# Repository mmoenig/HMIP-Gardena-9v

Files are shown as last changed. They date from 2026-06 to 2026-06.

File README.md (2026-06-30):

# Homematic IP Steuerung eines Gardena 9V Ventil

## Problem das gelöst werden soll

- Die Gardena Bewässerungscomputer mit Bluetooth lassen sich nicht zuverlässig mit dem Handy steuern.
- Die Bodenfeuchte-Sensoren die an den Ventilen angeschlossen sind funktionieren ebenfalls nicht zuverlässig. z.B. wird an Regentagen ein trockener Boden gemessen und dadurch noch zustzlich bewässert und auch in die andere Richtung wird an heissen Tagen nicht zuverlässig bewässert
- Unterschiedliche Systeme erhöhen die Komplexität und die Übersicht im SmartHome
- Gardena ist mit diesem System nicht offen und in kein anderes System integrierbar.

## High Level Requirements

- Ein Gardena 9V-Latchventil soll über das Homematic IP ansprechbar sein. 
- Die Automatisierung erfolgt (An/Ausschalten) erfolgt außerhalb dieser Schaltung über entsprechende HMiP Automatisierung
- Die Schaltung muss mit 4 AA-Zellen für 6 Monate lauffähig sein (Garten-Saison)
- Die Ganze Elektronik soll in einer relativ kleinen Abzweigdose (Spelsberg Abox 025) untergebracht werden
- Die Schaltung soll nur für ein einzelnes Ventil sein

## Hardware Komponenten

Die Steuerung basiert auf:

* [Homematic IP HMIP-PCBS-BAT als Funkmodul](hardware/hmippcbsbat/hmippcbsbat.md)
* [Gardena 9V Ventil](hardware/gardena/gardena.md)
* [ATtiny85 als Steuerlogik](hardware/ATtiny85/attiny85.md) 
* [DRV8833 als H-Brücke](hardware/drv8833/drv8833.md)
* [MT3608 als Step-up Wandler](hardware/mt3608/mt3608.md)
* [Spelsberg Abox 025 als Gehäuse](hardware/abox025/abox025.md)
* 4× AA Batterieversorgung (LifePo4)

## Materialliste

| Pos. | Bauteil | Typ / Wert | Menge | Bemerkung |
| ---: | --- | --- | ---: | --- |
| 1 | Funk-Schaltaktor | HmIP-PCBS-BAT | 1 | Homematic IP Schaltplatine |
| 2 | Mikrocontroller | ATTiny85-20PU | 1 | DIP-8 Sockel |
| 3 | Motortreiber | [DRV8833 Modul](https://www.amazon.de/DRV8833-2-Kanal-DC-Motorantriebsplatine-Motorantriebs-Eingangsspannung/dp/B0DHRFRG6X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) | 1 | H-Brücke für Polaritätsumkehr |
| 4 | Step-Up-Wandler | [MT3608 Modul](https://www.amazon.de/Converter%EF%BC%8CEinstellbare-Spannungsreglerplatine-Power2V-24V-V%EF%BC%8CNetzteil-Kompatibel/dp/B0D9VJKD1L/) | 1 | Eingang 4–6 V, Ausgang 9 V |
| 5 | Bewässerungsventil | Gardena 01815-00.707.00 | 1 | Hydraulikventil mit Cinch-Anschluss |
| 6 | Batteriehalter | 2× AA | 2 | 1 x HMIP und 1 x Lastkreis (DRV8833,ATTiny,MT3608) |
| 7 | Batterie | [AA LiFePO4, 3.2V 600mAh](https://www.amazon.de/POWJIELI-Wiederaufladbarer-Selbstentladung-Solar-Gartenleuchten-Solarpfostenleuchten/dp/B0FLWY2FXT) | 4 | Versorgung |
| 8 | Widerstand | 10 kΩ | 1 | Pull-Up für HmIP-Ausgang |
| 9 | Widerstand | 47 Ω | 1 | Strombegrenzung Schließimpuls |
| 10 | Diode | 1N4001 | 1 | Überbrückung des 47-Ω-Widerstands |
| 11 | Kondensator | 670 µF / ≥16 V | 1 | MT3608 Eingang |
| 12 | Kondensator | 100 µF / ≥16 V | 1 | DRV8833 Versorgung |
| 13 | Kondensator | 100 nF | 2 | DRV8833 und ATTiny85 |
| 14 | IC-Sockel | DIP-8 | 1 | Für ATTiny85 |
| 15 | Terminal-Anschlussblock | [10 alt. 12 fach, 2.54](https://www.amazon.de/10Pcs-Terminal-Block-Steckverbinder-Schraubklemmenblock/dp/B07BVPJBK3) | 1 | Gardena Ventil, Batterie, HMIP |
| 17 | Gehäuse | Spelsberg ABOX 025 | 1 | Endmontage |
| 18 | Lochrasterplatine  | 24 Spalten (A–X),2.54 | 1 | Individuell zuschneiden |
| 19 | Silberdraht | 0,14–0,25 mm² | nach Bedarf | Verdrahtung |
| 20 | Schrumpfschlauch | verschiedene Größen 1,5 / 3.5 /4.0 | nach Bedarf | Isolation |

## Schaltung - Komponentensicht

### Gardena Aktor
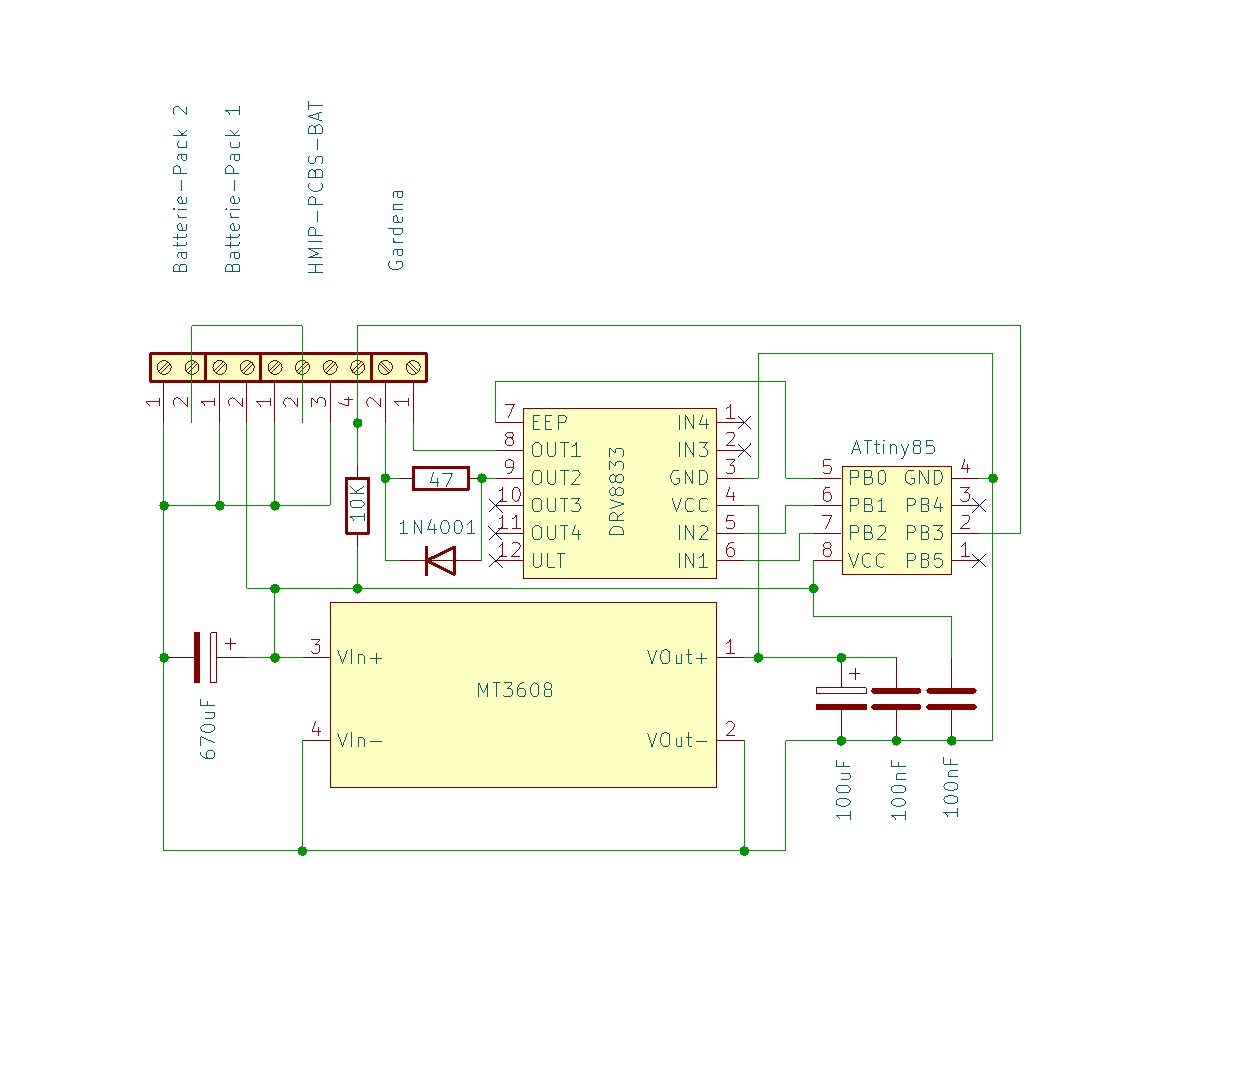
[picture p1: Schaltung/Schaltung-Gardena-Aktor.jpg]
Schaltung-Aktor


### Homematic IP
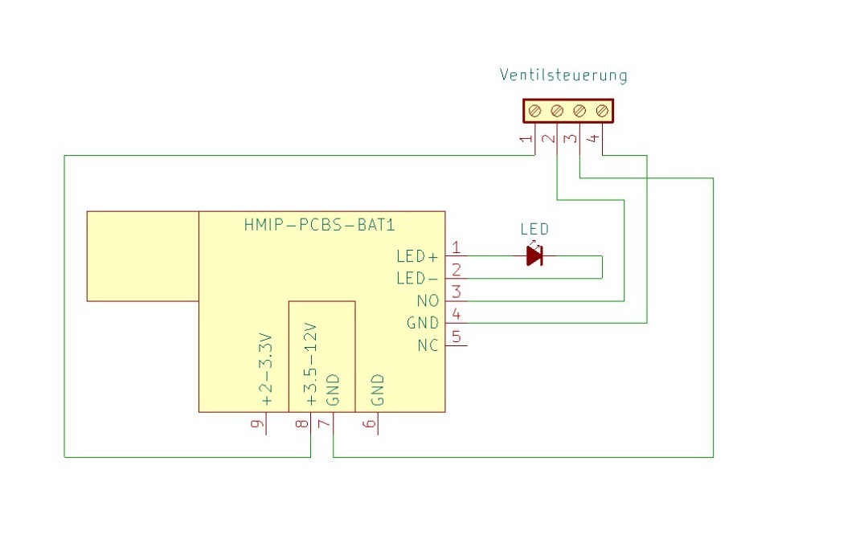
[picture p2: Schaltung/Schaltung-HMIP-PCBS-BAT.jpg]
Schaltung-HMIP


## Architektur
~~~
                    Gemeinsame Masse (GND)
                           │
        ┌──────────────────┴──────────────────┐
        │                                     │

   Batteriepack 1                       Batteriepack 2
      (Logik)                            (Leistung)
      2×AA / 6–7 V                       2×AA / 6–7 V
        │                                     │
        │                                     ├──────── ATTiny85
        │                                     ├──────── MT3608
        │                                     │
        │                                     └── MT3608 ── 9 V ── DRV8833 ── Gardena Ventil
        │
        └──────── HmIP-PCBS-BAT

HmIP Open-Drain Ausgang ───────────────► PB3 (ATTiny)
~~~

## Funktionsprinzip

Das Homematic-IP-Modul liefert ein digitales Open-Drain-Triggersignal an den ATTiny85.

Der ATTiny85 überwacht den Eingang kontinuierlich und erkennt jede Zustandsänderung (LOW→HIGH bzw. HIGH→LOW). Abhängig von der Richtung der Zustandsänderung erzeugt er einen kurzen Steuerimpuls:

Öffnen: 60 ms
Schließen: 250 ms

Der DRV8833 arbeitet als H-Brücke und kehrt für jeden Steuerimpuls die Polarität um. Dadurch kann das bistabile 9-V-Gardena-Magnetventil sowohl geöffnet als auch geschlossen werden.

## Stromversorgung

### Batterieversorgung

| Versorgung | Spannung | Versorgt |
| --- | --- | --- |
| Batteriepack 1 | 2× LiFePO₄ (6,0–7,2 V) | ATTiny85, MT3608, DRV8833 |
| Batteriepack 2 | 2× LiFePO₄ (6,0–7,2 V) | HmIP-PCBS-BAT |

### Spannungsverteilung

| Komponente | Versorgung |
| --- | --- |
| ATTiny85 | direkt aus Batterie |
| HmIP-PCBS-BAT  | direkt aus Batterie |
| MT3608 Eingang | direkt aus Batterie |
| DRV8833 | 9V vom MT3608 |
| Ventil | 9V vom DRV8833 |

### Masseverteilung

Eine gemeinsame Masse - keine getrennten Massebereiche erforderlich.
~~~
Batteriepack 1 (+6 V)
    │
    ├── ATTiny85
    ├── MT3608
    └── DRV8833

Batteriepack 2 (+6 V)
    │
    └── HmIP-PCBS-BAT

Gemeinsame Masse (GND)
    ├── Batteriepack 1
    ├── ATTiny85
    ├── MT3608
    ├── DRV8833
    ├── HmIP-PCBS-BAT
    └── Batteriepack 2
~~~

## MT3608 Step Up Wandler

Der MT3608 erhöht die Batteriespannung auf 9V für:

- DRV8833
- Gardena-Ventil

| Parameter | Wert |
| --- | ---- |
| Ausgangsspannung | 9V |

**WICHTIG*** 
Vor Inbetriebnahme die Ausgangsspannung mit Multimeter einstellen!

## HmIP-PCBS-BAT Homematic IP Funkmodul

Das Modul liefert ein Open-Drain-Schaltsignal an den ATTiny85.

| Zustand | Ausgang |
| --- | --- |
| aktiv | LOW |
| inaktiv | offen |

### Pin Belegung

| Pin | Funktion | Verbindung |
| --- | --- | --- |
| NO | Open-Drain-Ausgang | Normally Open, ATTiny85 PB3, 10 KOhm Pullup Widerstand gegen VCC |
| NOC | Open-Drain-Ausgang | - |
| GND | Masse | gemeinsame Masse |
| +3.5-12V | Versorgung | Batteriespannung |
| LED+ | LED | LED + |
| LED- | LED | LED - |

### Schaltung
~~~
6.4V (VCC)
 │
 └── 10kΩ
       │
       ├──── ATTiny85 PB3
       │
HmIP-PCBS-BAT OUT
       │
      GND
~~~

## ATTiny85 Steuerlogik

Der ATTiny85 übernimmt:

- Flankenerkennung
- Impulssteuerung
- Polaritätssteuerung
- Sleep-Modus

### Pin Belegung

| ATTiny85 Pin | Port | Funktion |
| --- | ---- | --- |
| 1 | PB5  | - |
| 2 | PB3  | Trigger Eingang |
| 3 | PB4  | - |
| 4 | GND  | Masse |
| 5 | PB0  | DRV8833 SLP/EEP |
| 6 | PB1  | DRV8833 IN2 |
| 7 | PB2  | DRV8833 IN1 |
| 8 | VCC  | 6.4V |

## DRV8833 H-Brücke

Der DRV8833 erzeugt:

- positive Polarität
- negative Polarität

für das bistabile Gardena-Ventil.

### Pin Belegung

| Pin | Funktion | Verbindung |
| ----- | --- | --- |
| VCC | Ventilversorgung  | 9V vom MT3608 |
| GND | Masse | gemeinsame Masse |
| IN1 | Richtung A | ATTiny85 PB2 |
| IN2 | Richtung B | ATTiny85 PB1 |
| IN3 | unbenutzt | - |
| IN4 | unbenutzt | - |
| OUT1  | Ventilanschluss A | Gardena 1 | 
| OUT2  | Ventilanschluss B | Gardena 2 |
| OUT3  | unbenutzt | - |
| OUT4  | unbenutzt | - |
| EEP | Sleep-Eingang | ATTiny85 PB0 |
| FAULT | Fehlerausgang | - |

### Schaltung

~~~
VCC ---- 100µF (Elko) ----- GND
  \
   \--- 100nF (Keramik) --- GND
~~~

- Elko zur Stabilisierung der 9V Versorgung
- Kermatik Kondesator kann sehr schnell reagieren zur Filterung von schnelle Spannungsspitzen, Schaltflanken, HF-Störungen

## Gardena 9V Ventil

## Ventil schließen

| Signal | Zustand |
| --- | --- |
| IN1 | LOW |
| IN2 | HIGH |
| Dauer  | 250 ms  |

## Ventil öffnen

| Signal | Zustand |
| --- | --- |
| IN1 | HIGH |
| IN2 | LOW |
| Dauer  | 60 ms |

## Software / Steuerungslogic ATtiny85

* [Software Page](./Software/Sketch.md)

## Design-Werkzeuge

- KiCad 10.0, Schaltungs-Entwurf, https://www.kicad.org/
- Ardunino IDE 2.3.9, Sketch Entwicklung, https://docs.arduino.cc/software/ide/
- Trimble Sketchup for Web, 3D Modell Entwicklung, https://app.sketchup.com/app
- BambuLab 2.7.1.57, Slicer, https://bambulab.com/en/download/studio
- Fritzing 1.0.7, Lochraster Design, https://fritzing.org/download/

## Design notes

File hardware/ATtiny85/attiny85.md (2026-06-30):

# Atmel 8-Bit-AVR-Mikrocontroller mit 8K Byte In-System programmierbarem Flash

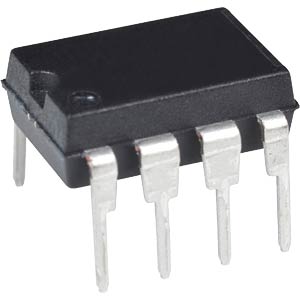
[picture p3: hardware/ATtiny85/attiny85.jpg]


## Merkmale:
- Hochleistungs-, stromsparender AVR® 8-Bit-Mikrocontroller
- Fortgeschrittene RISC-Architektur
- 120 leistungsstarke Anweisungen - die meisten Ein-Takt-Zyklus-Ausführungen
- 32 x 8 Arbeitsregister für allgemeine Zwecke
- Vollständig statischer Betrieb
- Nichtflüchtige Programm- und Datenspeicher
- 8K Byte systeminterner programmierbarer Programmspeicher Flash, 10.000 Schreib-/Löschzyklen
- 512 Bytes In-System programmierbares EEPROM, 100.000 Schreib-/Löschzyklen
- 512 Bytes interner SRAM
- Programmiersperre für selbstprogrammierendes Flash-Programm und EEPROM-Datensicherheit

### Periphere Merkmale
- 8-Bit-Timer/-Zähler mit Vorteiler und zwei PWM-Kanälen
- 8-Bit-Hochgeschwindigkeits-Zeitgeber/-Zähler mit separatem Vorteiler
- 2 Hochfrequenz-PWM-Ausgänge mit getrennten Ausgangs-Vergleichsregistern
- Programmierbarer Totzeit-Generator
- USI - Universelle serielle Schnittstelle mit Startbedingungsdetektor
- 10-Bit-ADC
- 4 Kanäle mit einem Ende
- Differentielle ADC-Kanalpaare mit programmierbarer Verstärkung (1x, 20x)
- Temperaturmessung
- Programmierbarer Watchdog-Timer mit separatem On-Chip-Oszillator
- On-Chip-Analogkomparator
- Industrieller Temperaturbereich

### Besondere Mikrocontroller-Merkmale
- debugWIRE On-chip-Debug-System
- Im System über SPI-Port programmierbar
- Externe und interne Interrupt-Quellen
- Niedrigleistungs-Leerlauf, ADC-Rauschunterdrückung und Abschaltmodi
- Erweiterte Power-on-Reset-Schaltung
- Programmierbare Brown-out-Erkennungsschaltung
- Intern kalibrierter Oszillator

### E/A und Bauformen
- Sechs programmierbare E/A-Leitungen
- 8-polige PDIP, 8-poliger SOIC, 20-poliges QFN/MLF

### Betriebsspannung
- 1,8 - 5,5V für ATtiny85V
- 2,7 - 5,5V für ATtiny85

### Geschwindigkeits-Grad
- ATtiny85V: 0 - 4 MHz bei 1,8 - 5,5V, 0 - 10 MHz bei 2,7 - 5,5V
- ATtiny85: 0 - 10 MHz bei 2,7 - 5,5V, 0 - 20 MHz bei 4,5 - 5,5V, 0 - 20 MHz bei 4,5 - 5,5V

### Leistungsaufnahme
- Aktiver Modus: 1 MHz, 1,8V: 300 µA
- Abschaltmodus: 0,1 µA bei 1,8V

## Pin Belegung
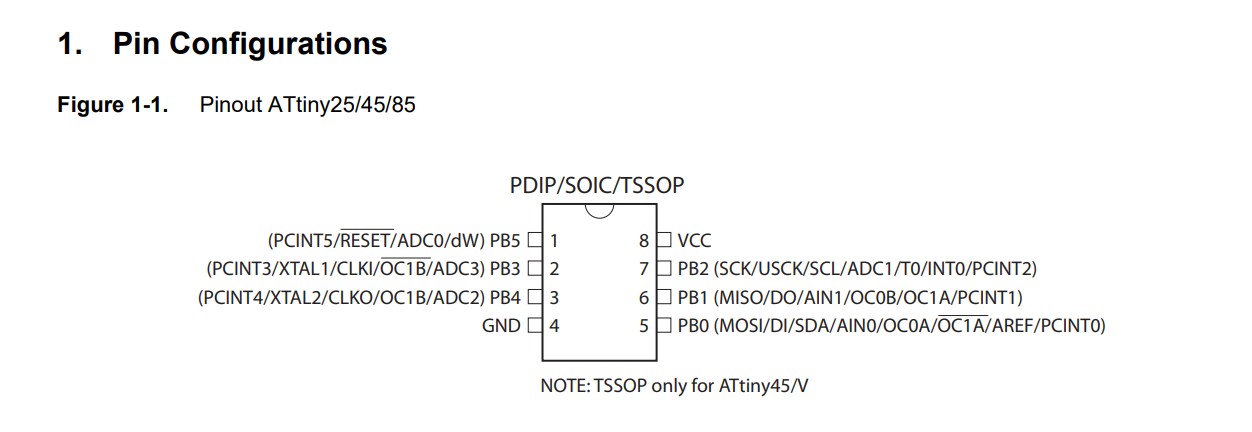
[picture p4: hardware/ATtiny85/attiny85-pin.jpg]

## Datenblatt
[Datenblatt](./attiny85.pdf)

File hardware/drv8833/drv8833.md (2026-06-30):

# DRV8833 1.5A 2-Kanal H Brücke DC-Motorantriebsplatine Ultra Small Volume Motorantriebs modul

- Der Motortreiber kann bei einem Konstantstrom von 1,0 A (4 A Spitze) bis zu zwei DC-Motoren steuern.
- Zwei Eingangssignale (IN1 und IN2) können verwendet werden, um den Motor in einem von vier Funktionsmodi zu steuern – Uhrzeigersinn (CW), gegen den Uhrzeigersinn (CCW), kurze Pause und Stopp.
- Eingebauter Überstromschutz, Kurzschlussschutz, Unterspannungsabschaltung und Übertemperaturschutz. Im Energiesparmodus.
- Die zwei Motorenausgänge (A und B) können separat gesteuert werden, die Geschwindigkeit jedes Motors wird über ein PWM-Eingangssignal mit einer Frequenz bis zu 100 kHz gesteuert.

## Netzstrom 
- VM = 2,7–10,8 V.
- Ausgangsstrom: Iout = 1,0 A (Durchschnitt) / 4 A (Spitze).

## DRV8833 Merkmale

| Eigenschaft | Wert |
| --- | --- |
| Versorgung VM | 2.7V – 10.8V |
| Sleep-Strom | typ. 1.6 µA |
| H-Brücken | 2 |
| Ausgangsstrom | 1.5A RMS / 2A Peak |
| Technologie | MOSFET |
| Polaritätsumkehr | ja |
| Schutzfunktionen | Überstrom, Temperatur, UVLO |
| Eingangskompatibilität | 3.3V / 5V GPIO |

## Datenblatt
[Datenblatt](./drv8833.pdf)

## Bilder
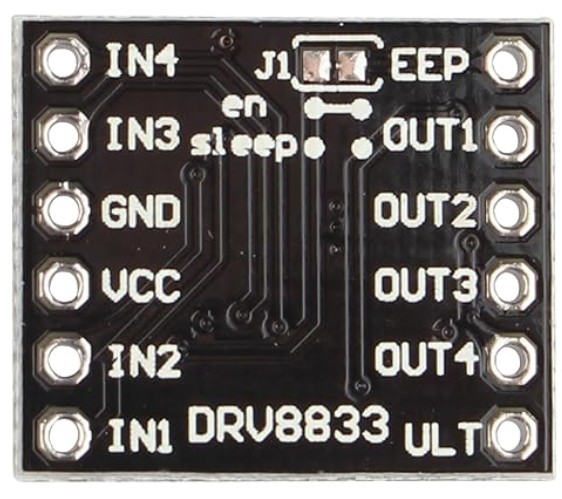
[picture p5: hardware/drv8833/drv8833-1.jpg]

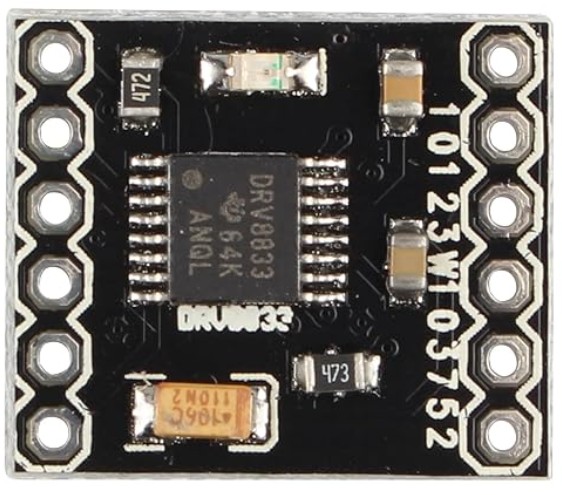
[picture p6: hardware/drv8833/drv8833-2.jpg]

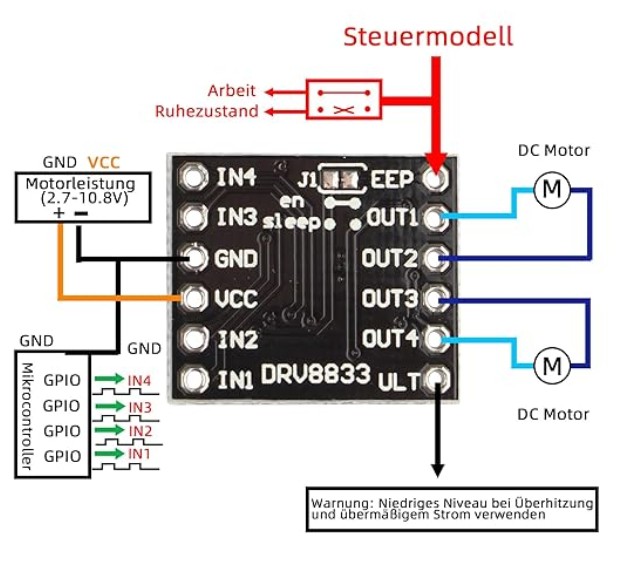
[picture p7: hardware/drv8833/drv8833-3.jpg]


## Pin Belegung

| Pin | Richtung | Funktion | Anschluss |
| ----- | --- | --- | --- |
| VCC | Eingang  | Versorgung DRV8833 (2.7–10.8V) | 9V vom MT3608 |
| GND | Eingang  | Masse | Gemeinsame GND |
| IN1 | Eingang  | Steuerung Kanal A Richtung 1 | ATTiny85 PB2 |
| IN2 | Eingang  | Steuerung Kanal A Richtung 2 | ATTiny85 PB1 |
| IN3 | Eingang  | Steuerung Kanal B Richtung 1 | - |
| IN4 | Eingang  | Steuerung Kanal B Richtung 2 | - |
| OUT1  | Ausgang  | Kanal A Ausgang 1 | Ventil 1 Leitung A |
| OUT2  | Ausgang  | Kanal A Ausgang 2 | Ventil 1 Leitung B |
| OUT3  | Ausgang  | Kanal B Ausgang 1 | - |
| OUT4  | Ausgang  | Kanal B Ausgang 2 | - |
| SLP | Eingang  | Sleep-Steuerung | ATTiny85 PB0. |
| FAULT | Ausgang  | Fehlerausgang | Optional / offen |

## Truth Table

(OUT1 und OUT2) sowie (OUT3 und OUT4) gehören fest zu einer H-Brücke und können nicht unabhängig voneinander verwendet werden.

| IN1 | IN2 | Ausgang |
| --- | --- | --- |
| 1 | 0 | OUT1=H / OUT2=L |
| 0 | 1 | OUT1=L / OUT2=H |
| 0 | 0 | Hi-Z / Coast |
| 1 | 1 | Brake |

| IN1  | IN2  | OUT1 | OUT2 |
| ---- | ---- | ---- | ---- |
| HIGH | LOW  | +9V  | GND  |
| LOW  | HIGH | GND  | +9V  |

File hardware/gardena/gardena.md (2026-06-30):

# Gardena 1251-20 9V Ventil

# Beschreibung

Das Bewässerungsventil ist bistabil, d.h. es benötigt einen Stromimpuls zum Öffnen und einen weiteren um wieder zu schließen.

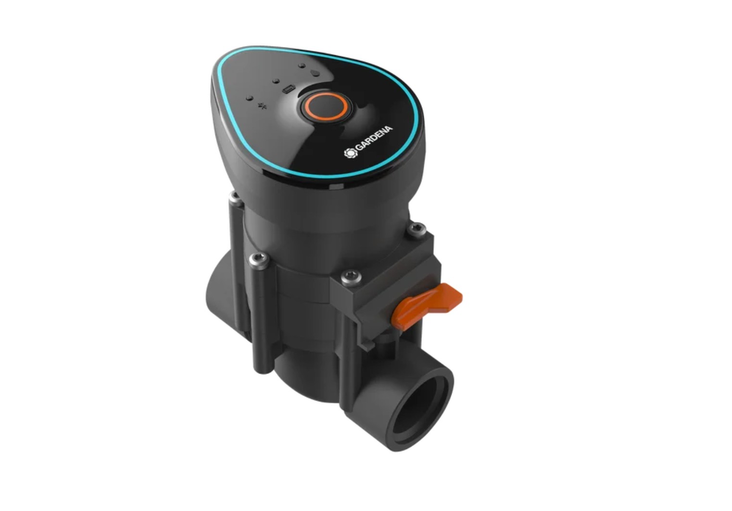
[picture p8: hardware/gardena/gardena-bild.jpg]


# Ansteuerung

Für Gardena 9 V bistabile Ventile gilt:

|Funktion |Spannung |Strom |Zeit |
|---|---|---|---|
|Öffnen	 |+9 V	 |~250–350 mA	 |~250 ms |
|Schließen |-9 V	 |~20–80 mA	 |~62,5 ms |

**Wichtig: Der Strom muss beim Schließen auf 80mA begrenzt werden sonst schließt das Ventil nicht!**

* [Gardena Technische Information](https://help.gardena.com/hc/de/articles/4450459219100-Welche-technischen-Daten-hat-das-9-V-Bew%C3%A4sserungsventil)

Die technischen Daten passen auch für die Bewässerungscomputer (Gardena Bluetooth) Artikel-Nr. 1889-20
- https://www.gardena.com/de/produkte/bewaesserung/bewaesserungssteuerung/bewaesserungssteuerung-bluetooth/970481101.html

# Dokumente

* [Ersatzteile](./gardena-ersatzteile.pdf)
* [Handbuch](./gardena-handbuch.pdf)
* [Ventil-Handbuch](./gardena-ventil.pdf)
* [Forum](https://homematic-forum.de/forum/viewtopic.php?f=19&t=2971#p15995)
* [Raspberry Forum](https://forum-raspberrypi.de/forum/thread/42577-umbau-gardena-bewaesserungsventil-1251-20-9v-auf-homematic/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)

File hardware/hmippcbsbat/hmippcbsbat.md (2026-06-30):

# Homematic IP Schaltaktor HMIP-PCBS-BAT für Batteriebetrieb

Baut man ein Smart Home Systems auf, steht man früher oder später unweigerlich vor der Aufgabe, eine Fernsteuerung weit ab von einer Netzstromversorgung ausführen zu wollen. Dann muss man auf Batterien, Akkus oder Solarzellen als Stromversorgung setzen. Genau dies ist der Einsatzort der neuen Schaltplatine für Batteriebetrieb. Aufgrund ihrer geringen Größe und ihres geringen Stromverbrauchs ist sie einfach in eigene Applikationen integrierbar.

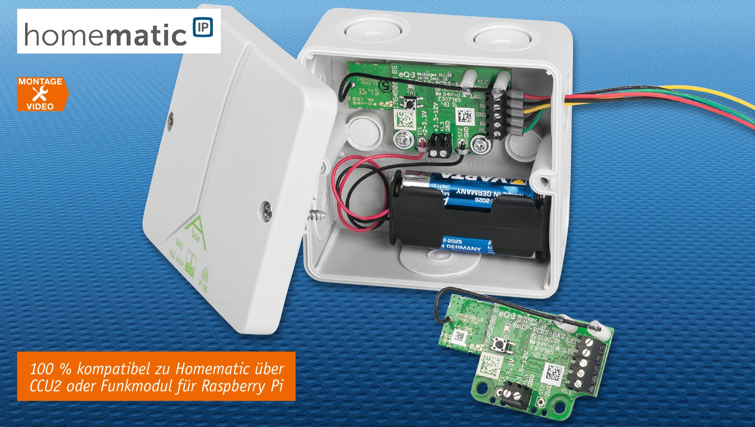
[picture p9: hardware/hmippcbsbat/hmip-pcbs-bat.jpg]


## Merkmale

| Eigenschaft | Wert |
| --- | --- |
| Geräte-Kurzbezeichnung | HmIP-PCBS-BAT |
| Versorgungsspannung | 2–3,3 VDC / 3,5–12 VDC |
| Stromaufnahme | max. 40 mA |
| Ausgänge | 2× Open-Drain 20 V / 3 A |
| Ausgangszustände | 1× in Ruhe offen / 1× in Ruhe geschlossen |
| Zusätzlicher Ausgang | 1× LED-Ausgang |
| LED-Betrieb | mit integriertem oder externem Vorwiderstand |
| Besonderheit | für stromsparenden Batterie-/Akkubetrieb optimiert |
| Leitungsart | starre oder flexible Leitung |
| Leitungsquerschnitt | 0,75–1,0 mm² |
| Maximale Leitungslänge | 3 m |
| Umgebungstemperatur | -10 bis +55 °C |
| Schutzklasse | III |
| Verschmutzungsgrad | 2 |
| Abmessungen (B × H × T) | 60 × 34 × 17 mm |
| Gewicht | 11 g |
| Funkmodul | TRX1-TIF |
| Funkfrequenzband | 868,0–868,6 MHz / 869,4–869,65 MHz |
| Funksendeleistung | max. 10 dBm |
| Empfängerkategorie | SRD category 2 |
| Typische Funkreichweite Freifeld | 250 m |
| Duty Cycle | < 1 % pro h / < 10 % pro h |

## Bilder

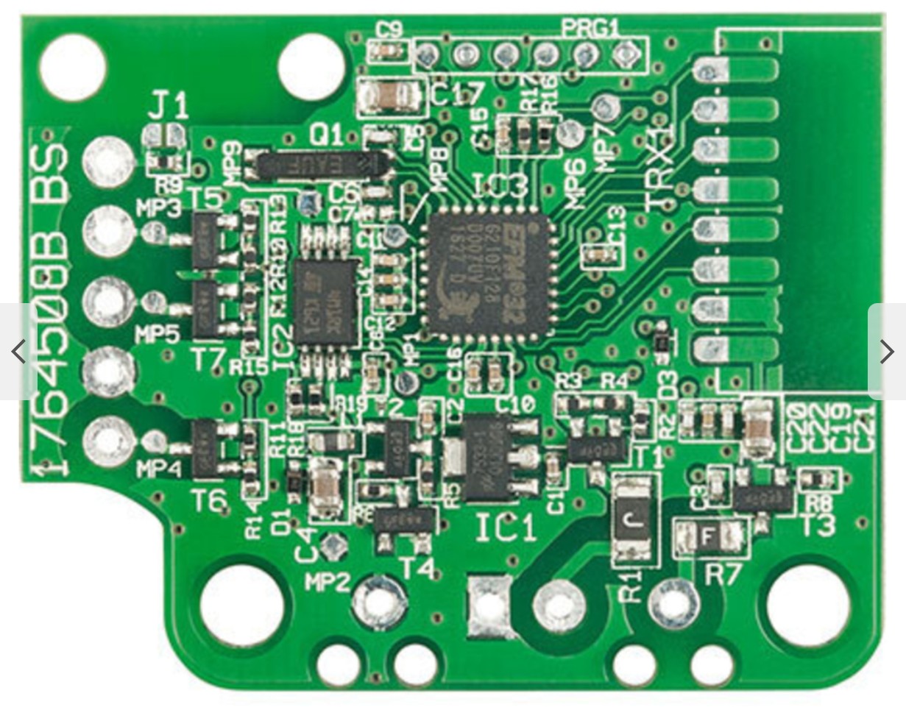
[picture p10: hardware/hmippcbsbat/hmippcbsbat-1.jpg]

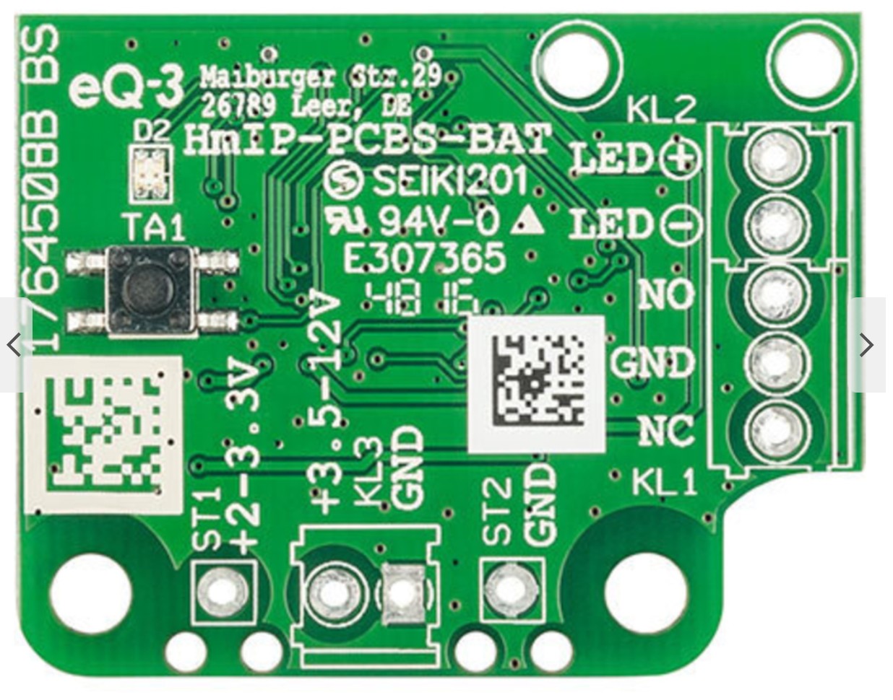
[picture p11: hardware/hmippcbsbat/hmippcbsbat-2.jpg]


## Schaltung

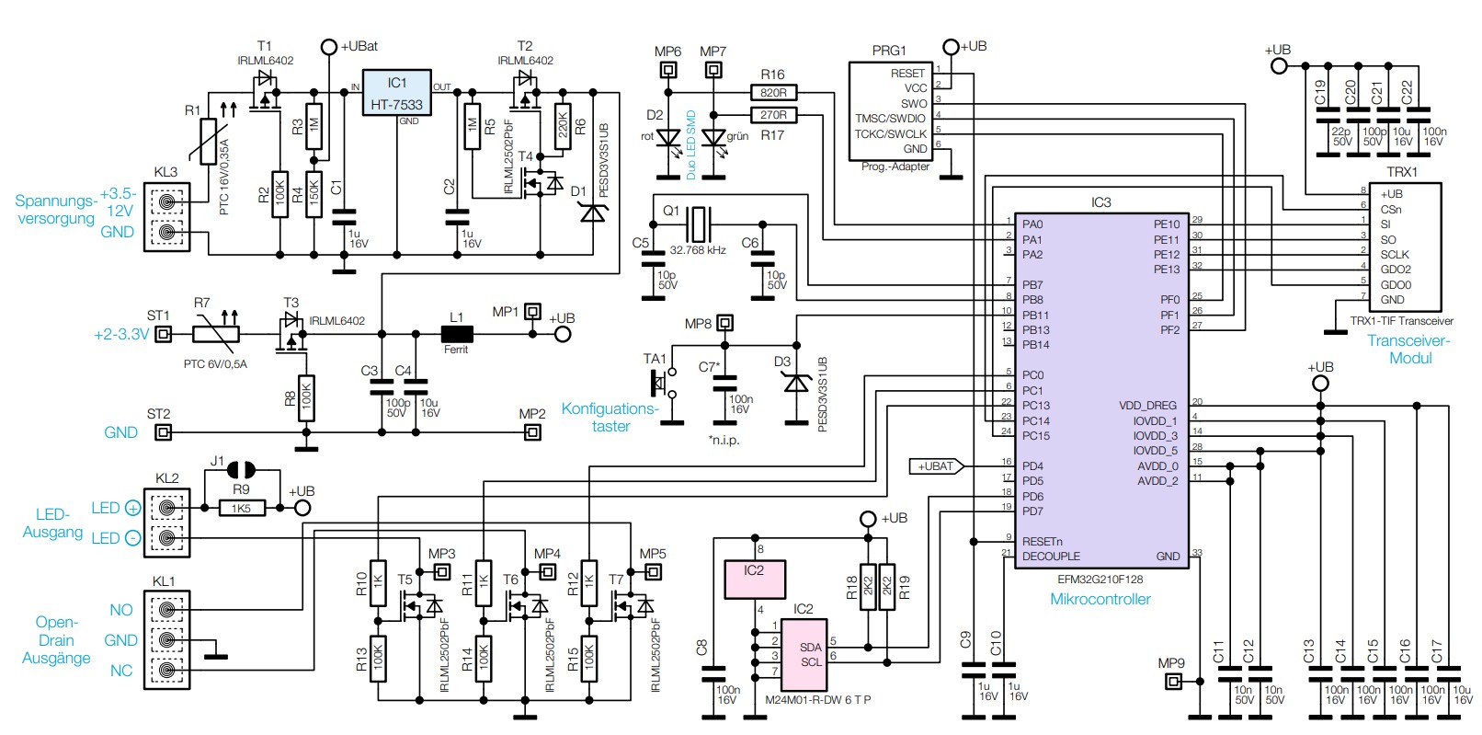
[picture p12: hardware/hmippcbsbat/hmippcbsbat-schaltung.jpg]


## Referenzen

- [ELV Produktseite](https://de.elv.com/p/homematic-ip-ganz-flexibel-schaltplatine-hmip-pcbs-bat-fuer-batteriebetrieb-P207141/?itemId=207141)
- [Schaltplan](./hmippcbsbat-schaltung.pdf)
- [ELV Artikel](./hmippcbsbat-journal.pdf)

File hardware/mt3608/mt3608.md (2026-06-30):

# MT3608 Mini DC-DC-Step up Wandler

Der MT3608 ist ein 2-A-DC/DC-Aufwärtswandlermodul (Boost-Wandler), das Eingangsspannungen von nur 2 V auf eine einstellbare Ausgangsspannung von bis zu 28 V hochwandeln kann. Es zeichnet sich durch einen Wirkungsgrad von 97 %, eine Schaltfrequenz von 1,2 MHz und eine integrierte Soft-Start-Technologie aus. Auch im Jahr 2026 gilt es aufgrund seiner geringen Kosten und des SOT-23-Formfaktors weiterhin als Goldstandard für die Stromversorgung von Arduino-, ESP32- und IoT-Projekten über Li-Ionen-Akkus.

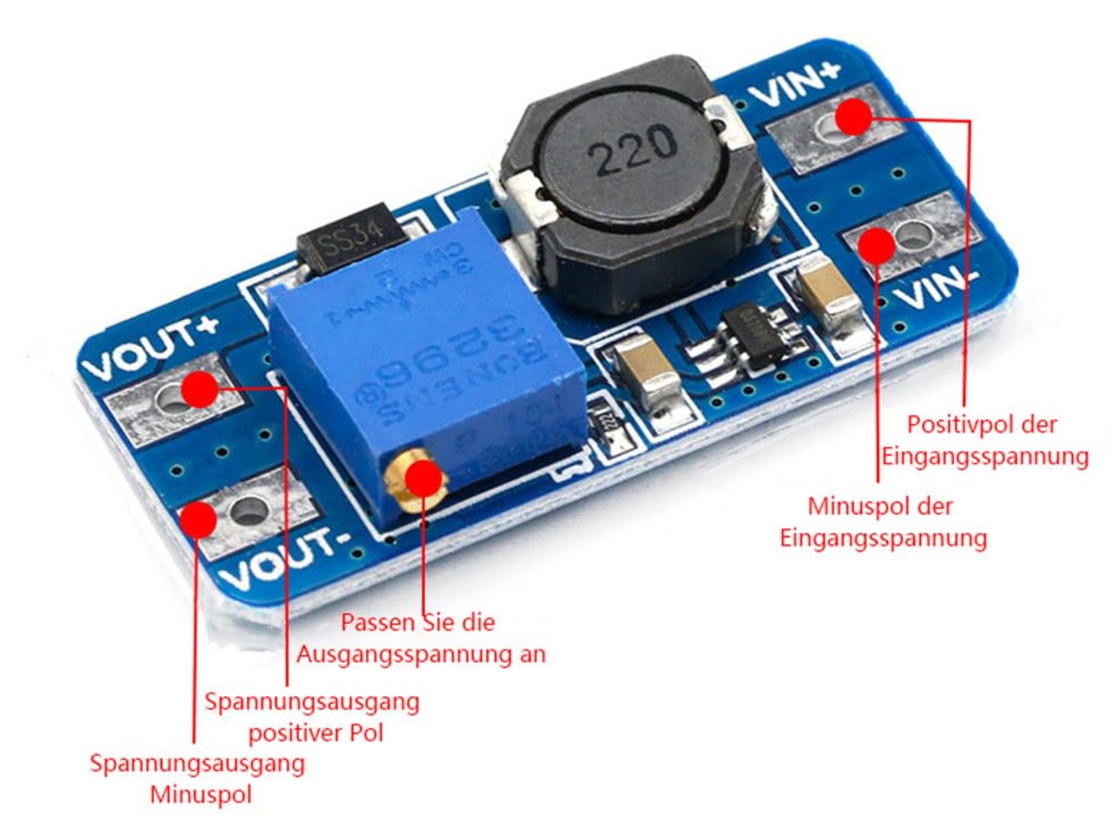
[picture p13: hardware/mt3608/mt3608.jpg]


## Technische Eigenschaften

| Eigenschaft | Wert |
| --- | --- |
| Typ | DC/DC Step-Up Converter |
| Funktion | Spannungsaufwärtswandler |
| Eingangsspannung | 2V – 24V |
| Ausgangsspannung | bis 28V |
| Ausgangsstrom | typ. bis 2A |
| Wirkungsgrad | bis ca. 93–97 % |
| Schaltfrequenz | 1.2 MHz |
| Ruhestrom | typ. 100–200 µA |
| Shutdown-Strom | typ. 0.1 µA |
| Schutzfunktionen | Überstrom, Übertemperatur, UVLO |
| Gehäuse IC | SOT23-6 |
| Regelung | PWM/PFM |

## Pinbelegung

| Modulanschluss | Funktion |
| --- | --- |
| VIN+ | Eingang + |
| VIN- | Eingang GND |
| VOUT+ | Ausgang + |
| VOUT- | Ausgang GND |

## Referenzen
- [mt3608 Datenblatt](./mt3608.pdf)

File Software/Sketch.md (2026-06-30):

# Software für die Gardena Ventilschaltung (ATtiny85)

* [ArduninoISP.ino](./ArdunioISP.ino)
* [HomematicIPGardena.ino](./HomematicIPGardena.ino)

Zusätzliche Boardverwalter URL für Arduino IDE:
- https://raw.githubusercontent.com/damellis/attiny/ide-1.6.x-boards-manager/package_damellis_attiny_index.json
- https://github.com/damellis/attiny

# Software flashen

## Vorbereitung Arduino IDE
### ATtiny libs in Arduino IDE hinzufügen

1. Arduino IDE (hier 2.3.9) starten
2. Datei > Einstellungen > Zusätzliche Boardverwalter-URLs auswählen. Oben genannte URL einfügen. > OK
3. Öffnen des Boardverwalters unter Werkzeuge > Board > Boardverwalter.
4. attiny von David A. Mellis (hier 1.0.2) installieren

### Arduino UNO als Programmierer einrichten

1. Arduino UNO mit USB an Rechner anschließen
2. Arduino IDE starten
3. Datei > Beispiele > ArduinoISP > ArduinoISP
4. Im Pulldown Menü Arduino UNO am entsprechenden COM Port auswählen
5. Sketch auf Arduino UNO hochladen

## Hardware vorbereiten
### Attiny für Flashvorgang verkabeln

Den ATtiny85 wird mit einem Arduino UNO als Programmierer (ISP) geflasht.
Dazu wird der ATtiny85 auf ein Breadboard gesteckt und folgende Pins mit dem Arduino UNO verbunden.

| Arduino Uno | ATTiny85 Pin |
| --- | --- |
| D10 | Pin 1 (RESET) |
| D11 | Pin 5 (PB0/MOSI) |
| D12 | Pin 6 (PB1/MISO) |
| D13 | Pin 7 (PB2/SCK)  |
| 5V | Pin 8 (VCC) |
| GND | Pin 4 (GND) |

Ein 10yF Elko muss zwischen Pin 1 und GND eingebaut werden.

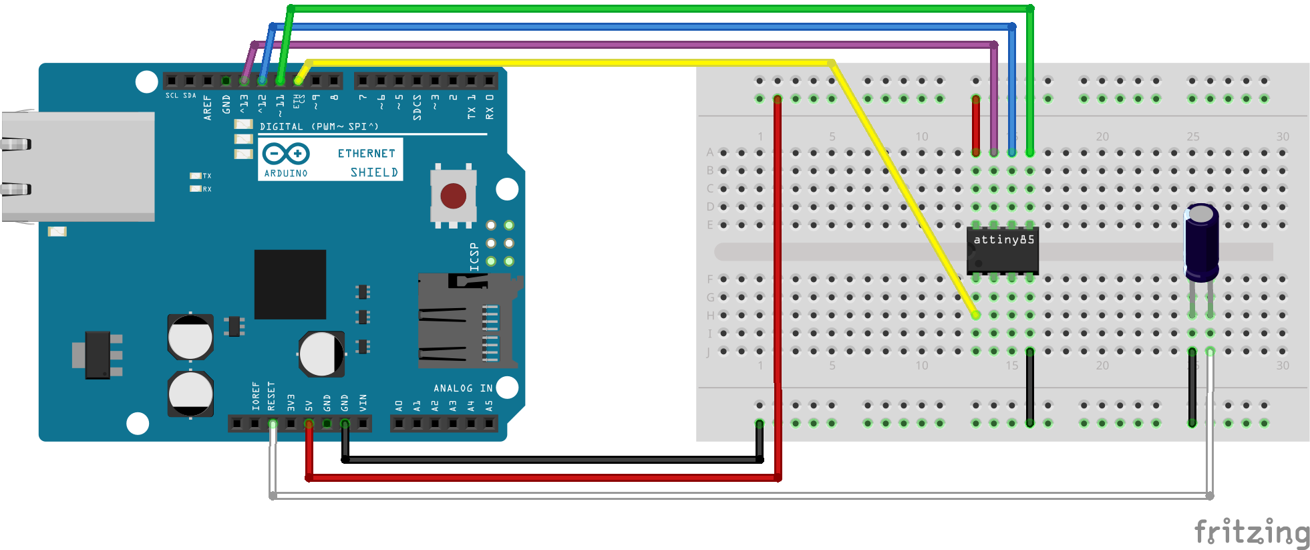
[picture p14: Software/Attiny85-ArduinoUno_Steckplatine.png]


## Software hochladen
### Program auf ATtiny85 schreiben

1. Arduino IDE öffnen und Gardena Sketch laden
2. Attiny25/45/85 Board am entsprechenden COM port auswählen
3. Taktfrequenz einstellen: Werkzeuge > Clock: Internal 1 MHz ausählen
4. Prozessor einstellen: Werkzeuge > Prozessor > ATtin85 auswählen
5. Programmier Methode einstellen: Werkzeuge > Programmer > ArduinoISP als Programmer auswählen
6. Upload durchführen: **Wichtig** Sketch > Mit Programmer hochladen

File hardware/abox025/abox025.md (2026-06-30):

# Spelsberg Abox 025

Abzweigkasten, mit Schutzart IP66, Nennquerschnitt 2,5 mm², zertifiziert durch VDE (DIN EN 60670-1/-22 (VDE 0606-1/-22)), DLG (Ammoniakbeständigkeit), selbstdichtende, weiche Einführungsmembranen, M16/M20, Dichtbereich 4 - 16 mm, (1 rückseitig, 8 seitlich), innenliegende Befestigungsstellen, für Standardinstallationen im Innenbereich und geschütztem Außenbereich

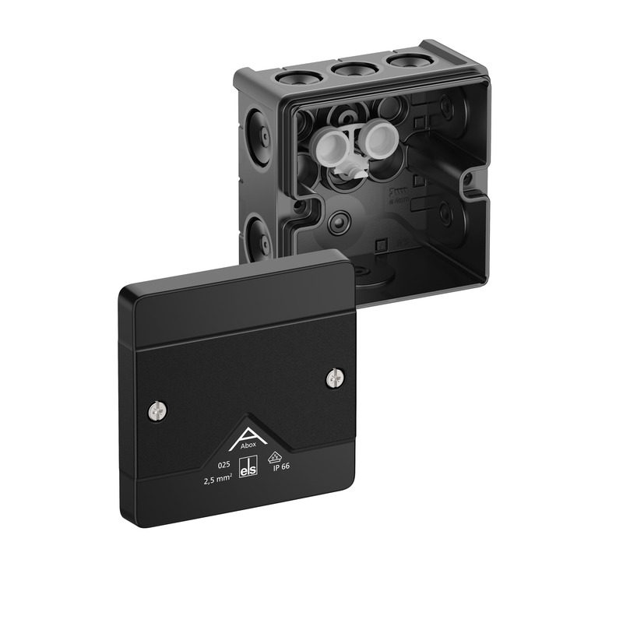
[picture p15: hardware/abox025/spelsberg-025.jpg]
Abox025


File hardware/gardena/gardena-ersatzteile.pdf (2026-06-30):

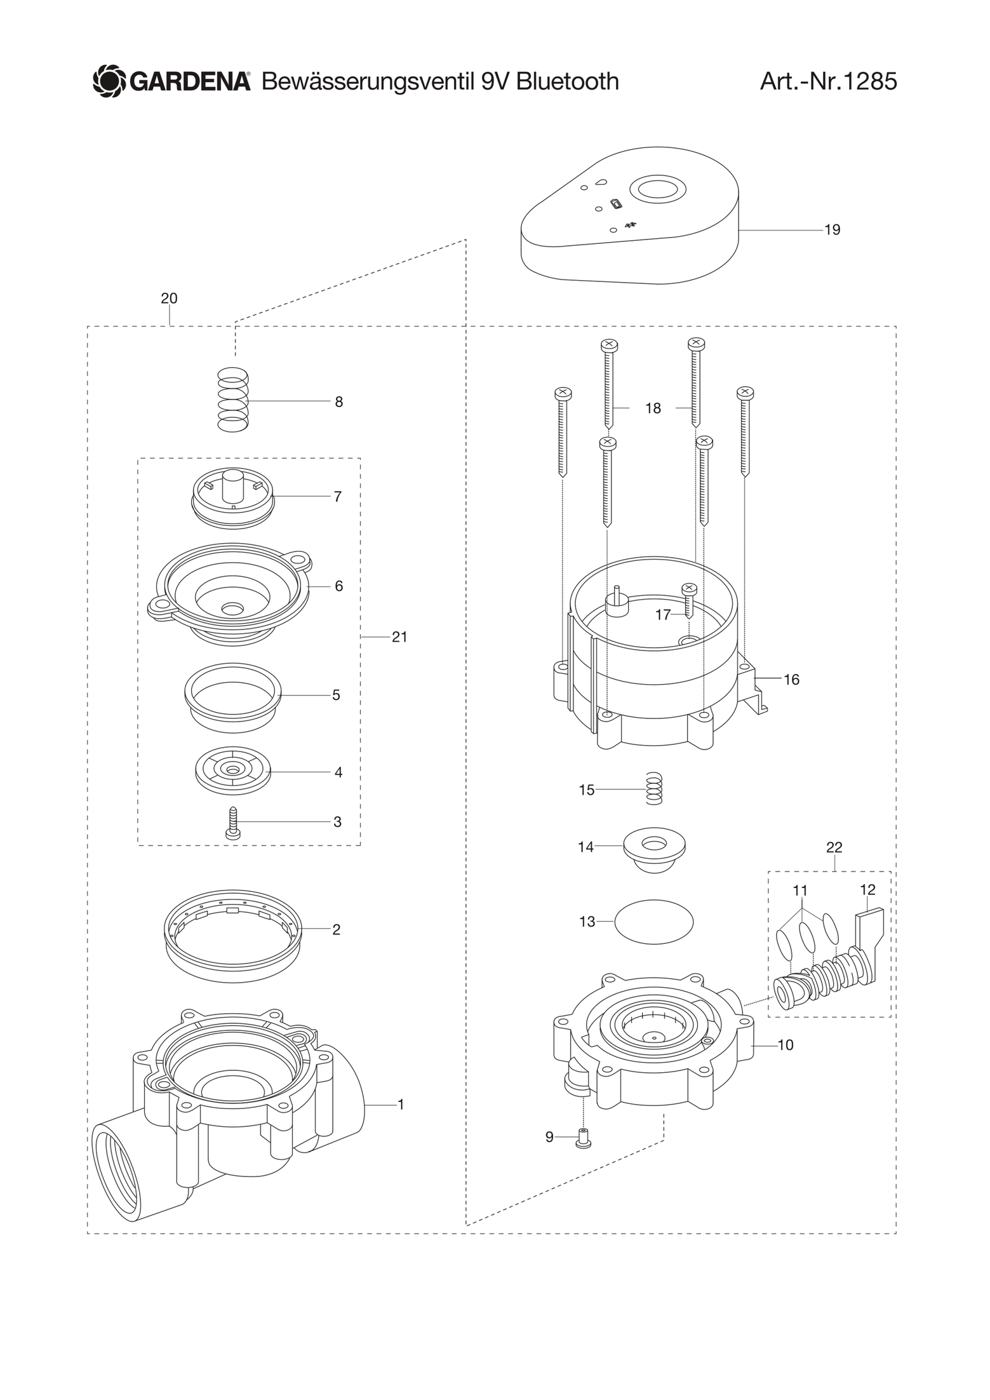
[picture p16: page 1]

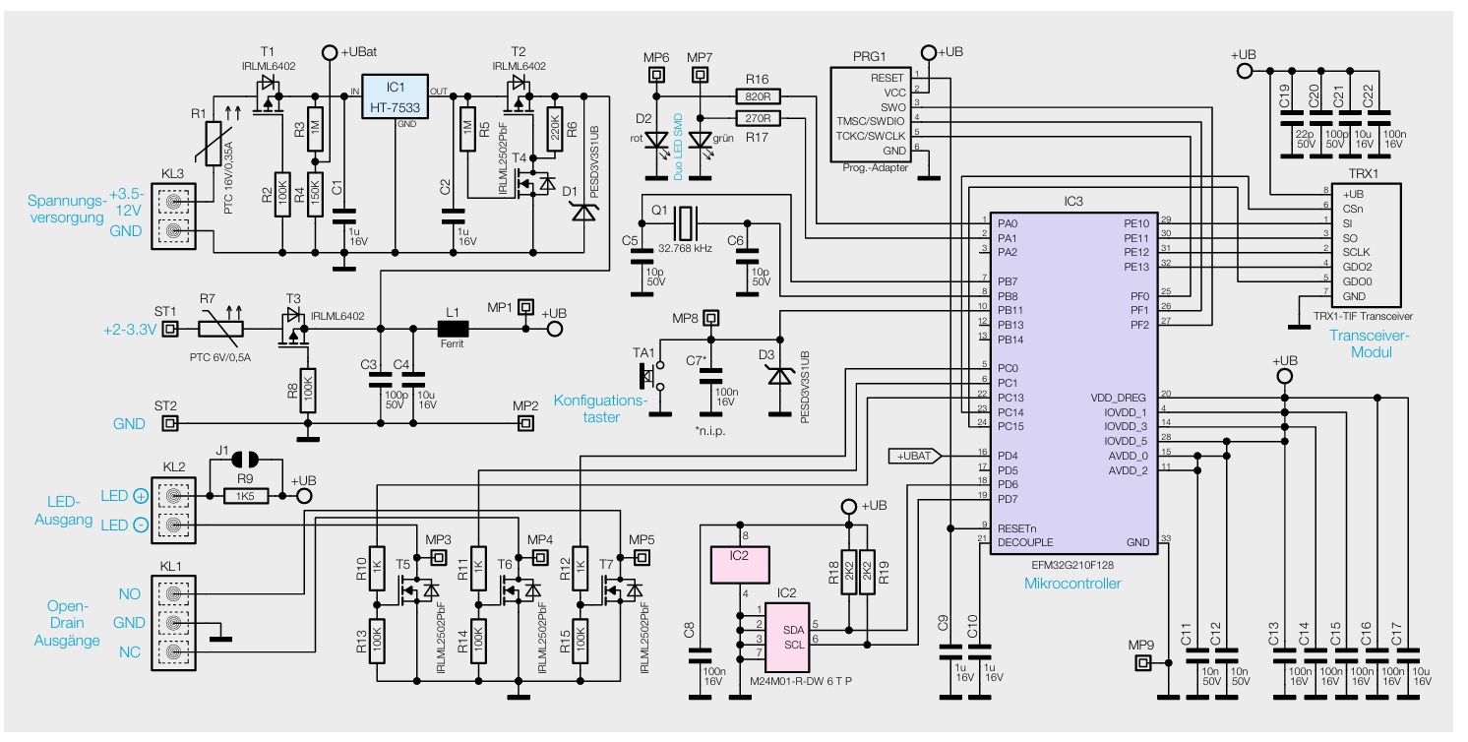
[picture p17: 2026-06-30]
hardware/hmippcbsbat/hmippcbsbat.jpg

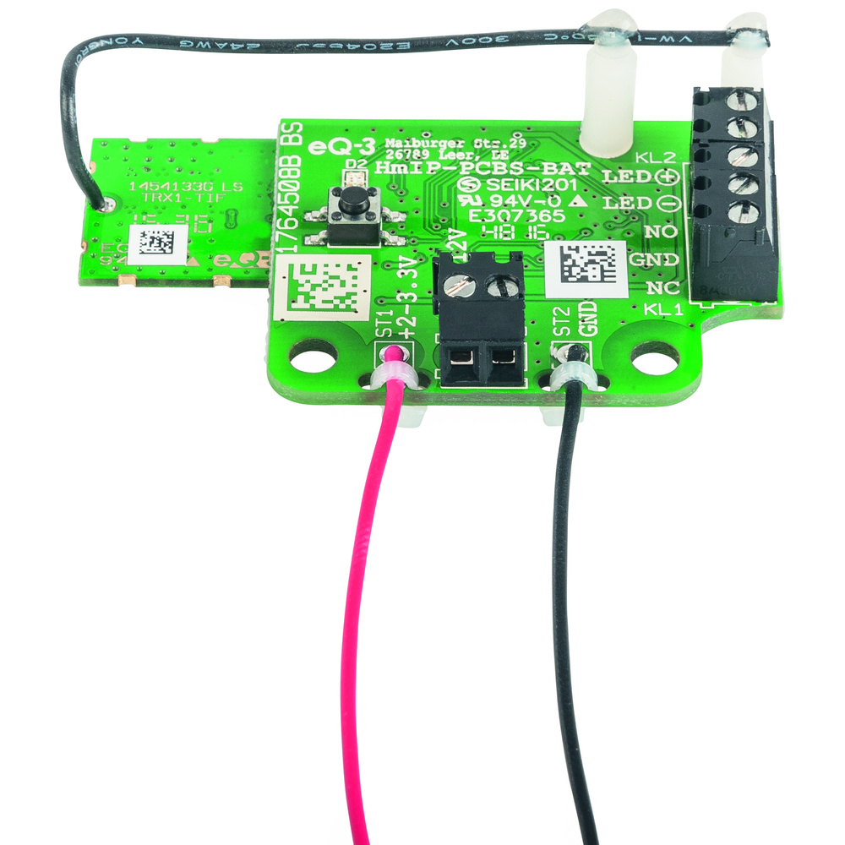
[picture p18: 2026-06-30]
hardware/hmippcbsbat/150904_f12_plhmip_pcbs.jpg

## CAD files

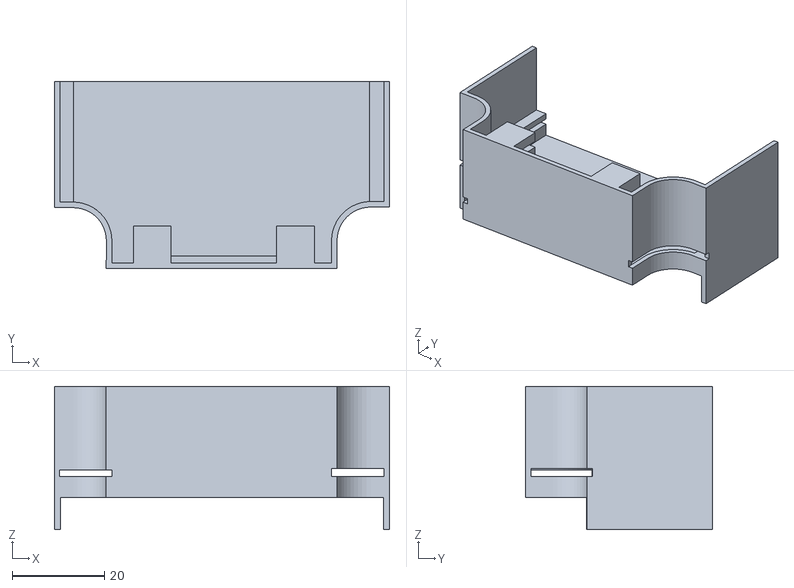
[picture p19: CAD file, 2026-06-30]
3D-Druck/Abox-025-Platinen-Halterung/abox-025-platinen-halterung.stl
72.6 x 40.5 x 31.1

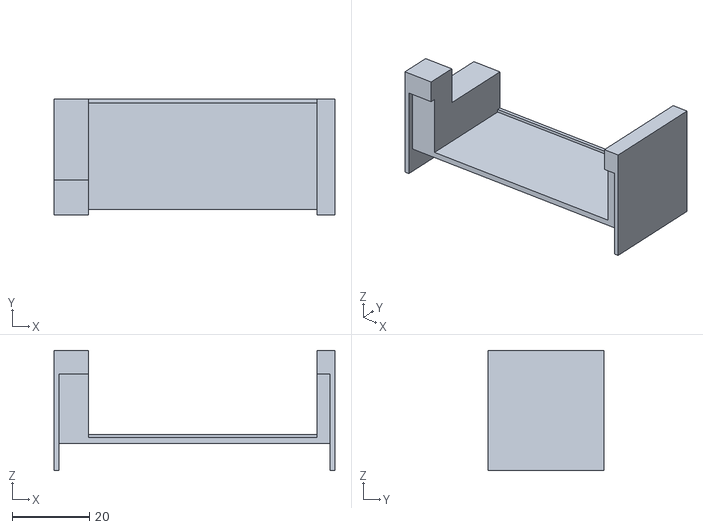
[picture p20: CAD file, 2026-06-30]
3D-Druck/Abox025-Batteriefach/Abox025-Batteriefach.stl
72.6 x 30.0 x 31.1

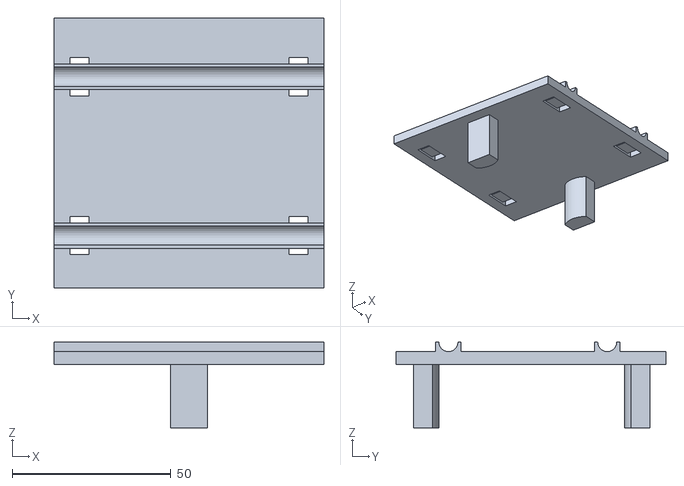
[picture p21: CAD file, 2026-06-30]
3D-Druck/Abox025-Befestigung-Zaun/Abox-025-Doppelstab-Platte.stl
85.0 x 85.0 x 27.0

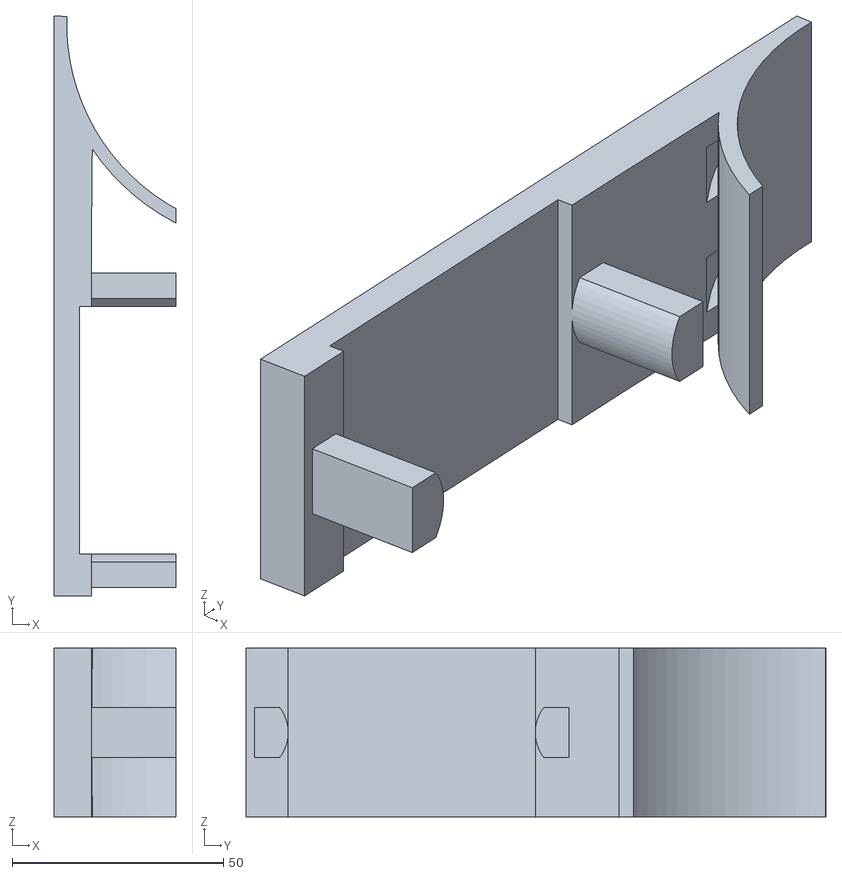
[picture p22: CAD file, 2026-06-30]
3D-Druck/Abox025-Halterung-Fallrohr/Abox025-Befestigung-DN100-Fallrohr.stl
28.8 x 137.3 x 40.0

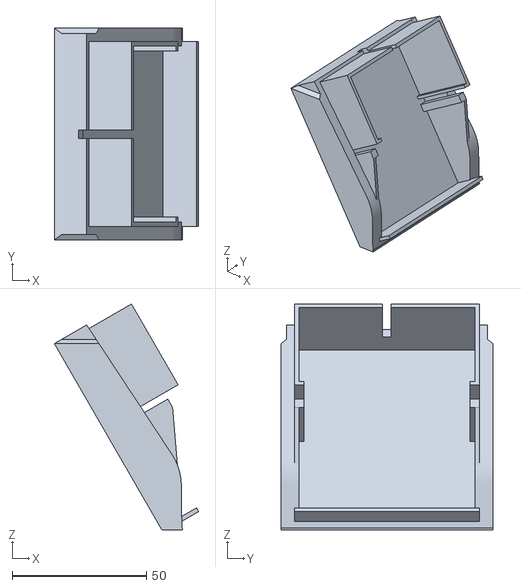
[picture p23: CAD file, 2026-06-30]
3D-Druck/Gardena-Ventil-Abdeckung/Gardena-Ventil-Abdeckung.stl
53.9 x 79.0 x 84.3

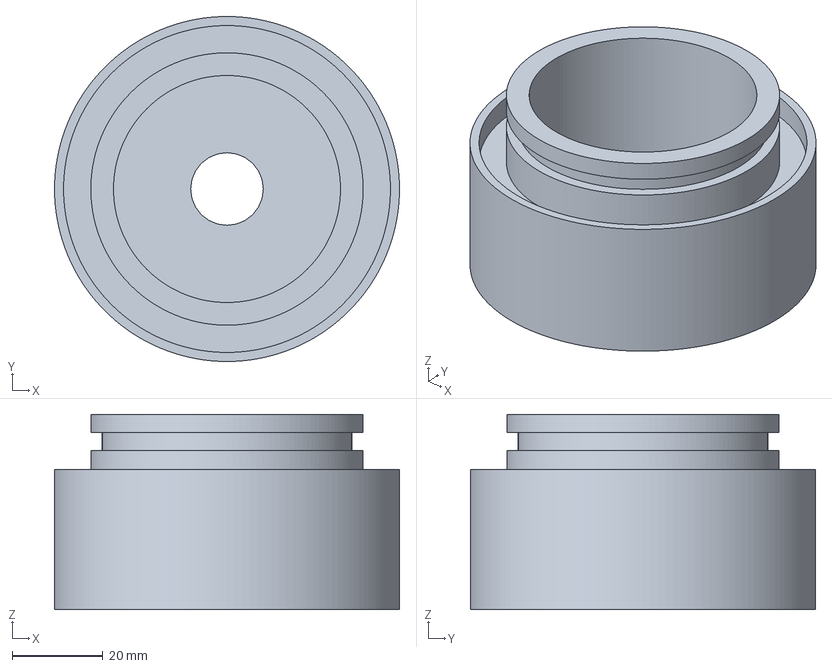
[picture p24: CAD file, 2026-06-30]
3D-Druck/Ventilbox/Gardena-9V-Ventil-Oberteil.3mf
76.0 x 76.0 x 43.0 mm

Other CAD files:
3D-Druck/Abox025-Halterung-Fallrohr/DN100-Fallrohr-Abox025.skp
3D-Druck/Gardena-Ventil-Abdeckung/Gardena-Ventil-Abdeckung.skp
3D-Druck/Ventilbox/Gardena-9V-Ventil-Oberteil.stl

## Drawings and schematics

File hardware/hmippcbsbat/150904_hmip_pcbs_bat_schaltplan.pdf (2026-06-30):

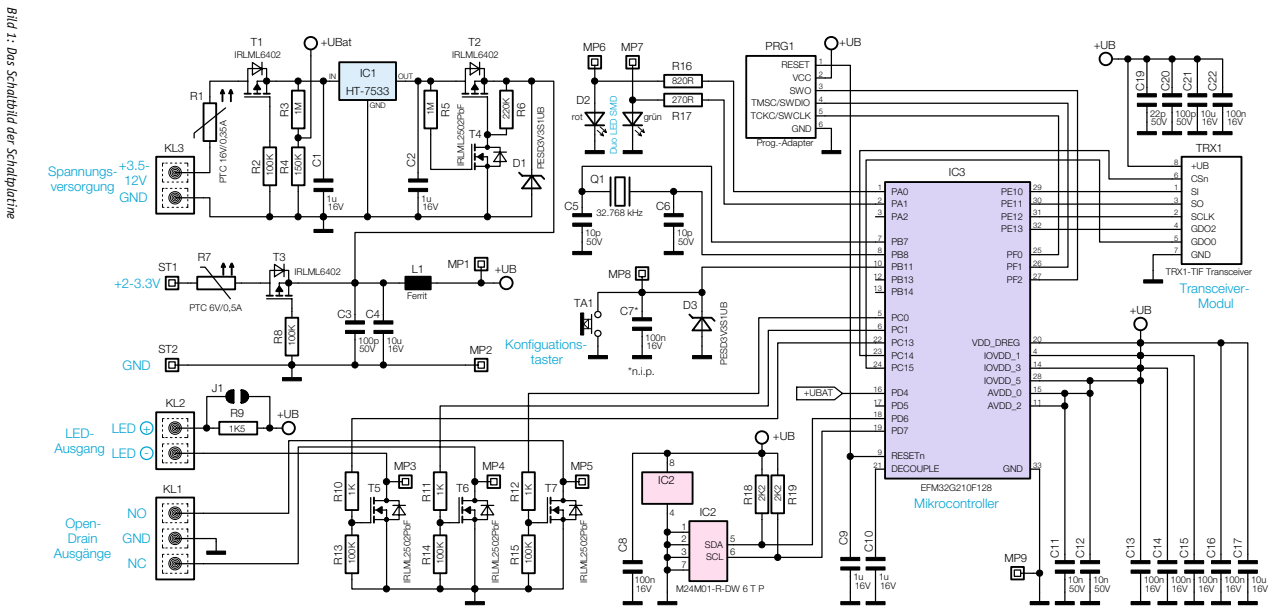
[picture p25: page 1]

Bild 1: Das Schaltbild der Schaltplatine

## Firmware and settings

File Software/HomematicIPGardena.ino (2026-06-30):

/*
 * Homematic IP Bewässerungssteuerung
 * (c) Markus Mönig, markus@moenig.online
 *
 * Hardware:
 * - ATTiny85
 * - DRV8833
 * - HmIP-PCBS-BAT
 * - Gardena 9V Latch-Ventil
 *
 * Pinbelegung:
 * PB0 -> DRV8833 SLP/EEP
 * PB1 -> DRV8833 IN2
 * PB2 -> DRV8833 IN1
 * PB3 -> HmIP-PCBS-BAT Ausgang
 */

// --------------------------------------------------
// Pin Definitionen
// --------------------------------------------------

const uint8_t PIN_DRV_SLEEP = 0;   // PB0
const uint8_t PIN_DRV_IN2   = 1;   // PB1
const uint8_t PIN_DRV_IN1   = 2;   // PB2
const uint8_t PIN_TRIGGER   = 3;   // PB3

// --------------------------------------------------
// Pulszeiten
// --------------------------------------------------

const uint16_t OPEN_TIME_MS  = 63;
const uint16_t CLOSE_TIME_MS = 250;

// --------------------------------------------------
// Status
// --------------------------------------------------

bool lastTriggerState;

// --------------------------------------------------
// Setup
// --------------------------------------------------

void setup()
{
    // DRV8833 Pins
    pinMode(PIN_DRV_SLEEP, OUTPUT);
    pinMode(PIN_DRV_IN1, OUTPUT);
    pinMode(PIN_DRV_IN2, OUTPUT);

    // Homematic Eingang
    pinMode(PIN_TRIGGER, INPUT_PULLUP);

    // DRV8833 initial schlafen
    digitalWrite(PIN_DRV_SLEEP, LOW);

    // Ausgänge sicher aus
    digitalWrite(PIN_DRV_IN1, LOW);
    digitalWrite(PIN_DRV_IN2, LOW);

    // Initialzustand lesen
    lastTriggerState = digitalRead(PIN_TRIGGER);
}

// --------------------------------------------------
// Hauptschleife
// --------------------------------------------------

void loop()
{
    bool currentState = digitalRead(PIN_TRIGGER);

    // Zustandsänderung erkannt
    if(currentState != lastTriggerState)
    {
        delay(10);

        currentState = digitalRead(PIN_TRIGGER);

        if(currentState != lastTriggerState)
        {
            // Homematic aktiv (LOW wegen Open Drain)
            if(currentState == LOW)
            {
                openValve();
            }
            else
            {
                closeValve();
            }

            lastTriggerState = currentState;
        }
    }

    delay(50);
}

// --------------------------------------------------
// Ventil öffnen
// --------------------------------------------------

void openValve()
{
    // DRV8833 aktivieren
    digitalWrite(PIN_DRV_SLEEP, HIGH);

    delay(5);

    // Polarität OPEN
    digitalWrite(PIN_DRV_IN1, HIGH);
    digitalWrite(PIN_DRV_IN2, LOW);

    delay(OPEN_TIME_MS);

    // Ausgänge deaktivieren
    digitalWrite(PIN_DRV_IN1, LOW);
    digitalWrite(PIN_DRV_IN2, LOW);

    // DRV8833 schlafen
    digitalWrite(PIN_DRV_SLEEP, LOW);
}

// --------------------------------------------------
// Ventil schließen
// --------------------------------------------------

void closeValve()
{
    // DRV8833 aktivieren
    digitalWrite(PIN_DRV_SLEEP, HIGH);

    delay(5);

    // Polarität CLOSE
    digitalWrite(PIN_DRV_IN1, LOW);
    digitalWrite(PIN_DRV_IN2, HIGH);

    delay(CLOSE_TIME_MS);

    // Ausgänge deaktivieren
    digitalWrite(PIN_DRV_IN1, LOW);
    digitalWrite(PIN_DRV_IN2, LOW);

    // DRV8833 schlafen
    digitalWrite(PIN_DRV_SLEEP, LOW);
}
